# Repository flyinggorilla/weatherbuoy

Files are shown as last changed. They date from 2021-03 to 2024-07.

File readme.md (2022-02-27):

# Weather Buoy - ESP32 4G/LTE Solar
* On-water solar powered autonomous wind and weather station
* ESP32, SIM7600E, GILL MaxiMet GMX501

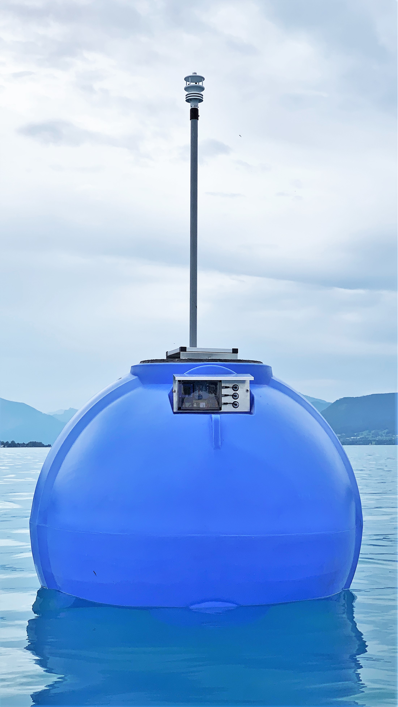
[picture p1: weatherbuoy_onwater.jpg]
weather buoy on water

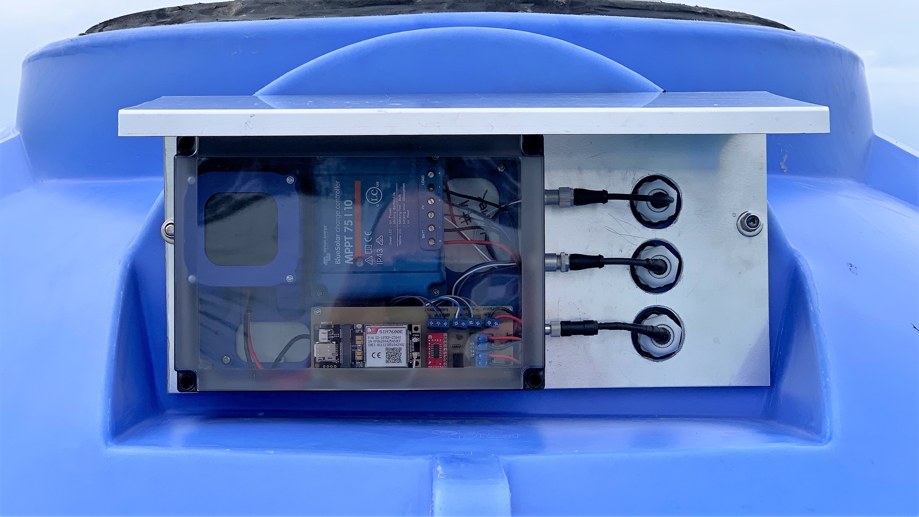
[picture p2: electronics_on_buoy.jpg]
electronics mounted on buoy with sun shield


<br>

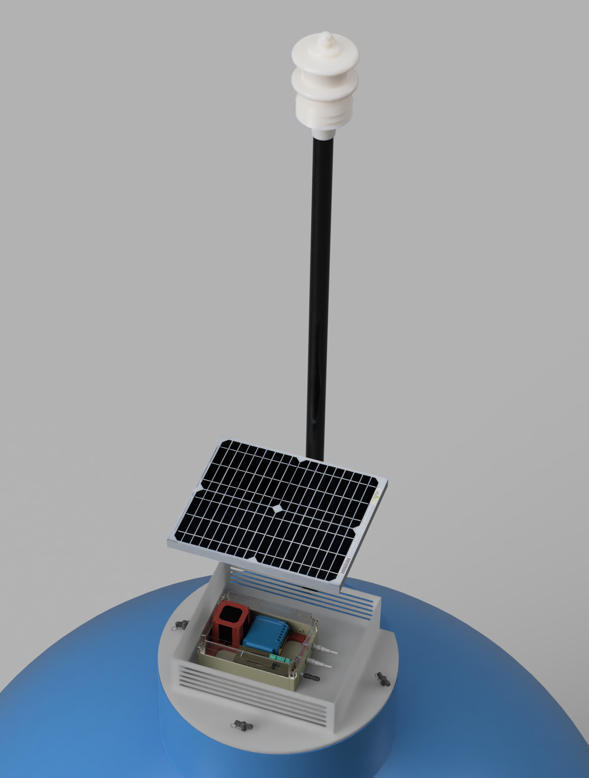
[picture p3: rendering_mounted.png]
rendering

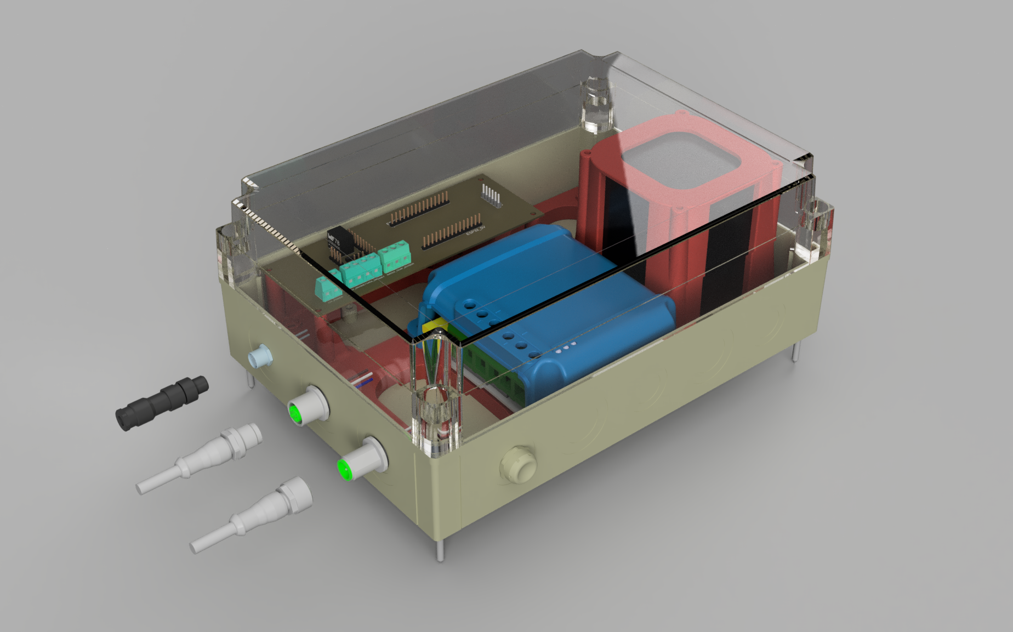
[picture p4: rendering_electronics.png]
rendering electronics

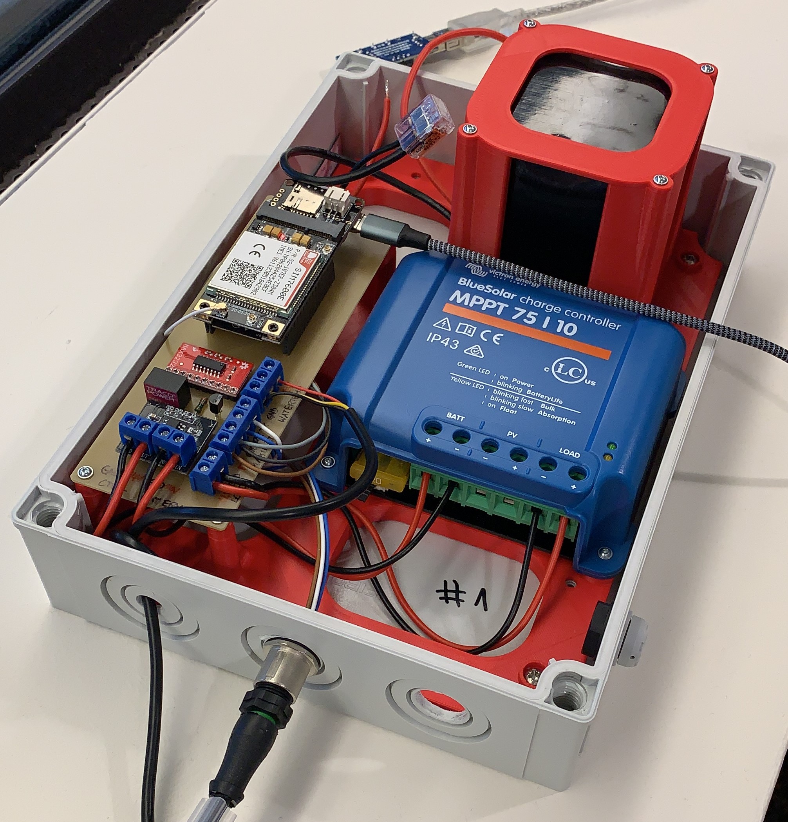
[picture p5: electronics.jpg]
electronics

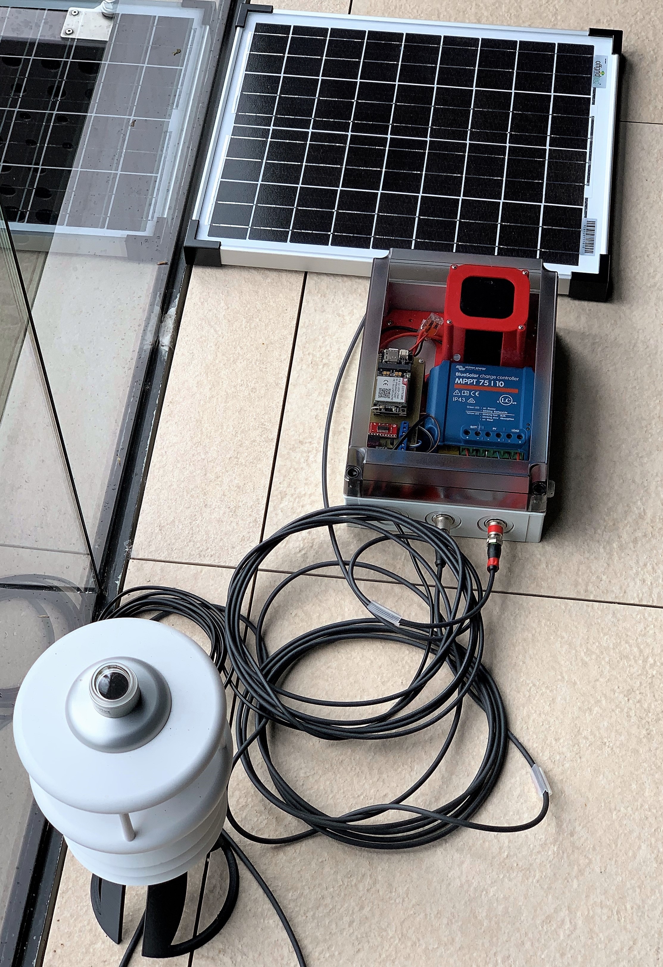
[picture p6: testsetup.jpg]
test setup
 

## Electronics part list

| Part | Description | Links | Cost (ex. delivery) |
|-|-|-|-|
| Waterproof housing | Fibox PCM200/100T, 255x180x100 Polycarbonat | [Fibox 6016927](https://www.fibox.de//catalog/64/product/183/6016927_GER1.html), [conrad](https://www.conrad.at/de/p/fibox-pcm-200-100-t-6016927-universal-gehaeuse-255-x-180-x-100-polycarbonat-lichtgrau-ral-7035-1-st-521203.html) | EUR 46 |
| Weather station | Gill MaxiMet: ultrasonic windspeed/direction, compass, solar radiation | [GILL MaxiMet GMX501](http://gillinstruments.com/data/datasheets/1957-009%20Maximet-gmx501%20Iss%207.pdf) Note: GMX200 costs half, just lacks solar| EUR 1500-3000 |
| Microcontroller |  Lilygo ESP32 | [LILYGO® TTGO T-PCIE ESP32-WROVER-B](http://www.lilygo.cn/prod_view.aspx?TypeId=50044&Id=1313&FId=t3:50044:3) | EUR 10 |
| 4G/LTE Modem  | SimCom 7600 | [PCIE-SIM7600E Module](http://www.lilygo.cn/prod_view.aspx?TypeId=50044&Id=1313&FId=t3:50044:3)  |  EUR 30 |
| Solar panel | 12V, 20W, monocrystalline, water proof IP65 | [Offgridtec](https://www.offgridtec.com/en/offgridtec-20w-mono-solarpanel-12v.html)| EUR 27 |
| Solar charging controller 12V | LiFePo4 capable, 5V power for microcontroller | [Victron Bluesolar, MPPT, 75/10](https://www.victronenergy.com/solar-charge-controllers/mppt7510) | EUR 80 |
| RS232 to TTL converter | MAX3232 to convert weatherstation's RS232 to 3.3V serial | [Sparkfun MAX3232 tranceiver breakout](https://www.sparkfun.com/products/11189) | EUR 5 |
| Voltage/Current sensor | MAX471 module, uses ESP32 ADC as there is no serial available to connect the ESP32 to the Victron Solar charger  | [MAX471 module with voltage divider](https://www.aliexpress.com/w/wholesale-max471-module.html), [MAX471 datasheet](https://www.maximintegrated.com/en/products/analog/amplifiers/MAX471.html) | ~EUR 2 |
| Water Temperature sensor | DS18B20 cable | [DS18B20 cable](https://www.az-delivery.de/en/products/2er-set-ds18b20-mit-3m-kabel?variant=19385240518752) | ~EUR 3 |
| On-Board Temperature sensor | DS18B20 TSO module | [DS18B20 TSO](https://www.az-delivery.de/en/products/5ersetds18b20?_pos=2&_sid=9a9ed3862&_ss=r) | ~EUR 1
| Battery | LiFePo4, 12V, 6Ah, 4S1P, including BMS | [Jubatec](https://www.jubatec.net/lifepo4-akku-12v-6ah-mit-bms-batterie-management-system_4652) | EUR 60 |
| 5V Power | convert ~14V Battery voltage to 5V for ESP32 |  [TracoPower TSR 1-2450 DC/DC-Wandler, 24V/DC 5V/DC 1A 6W](https://www.tracopower.com/int/model/tsr-1-2450) | EUR 6 |
| M12 male front-mount | Solar panel power, 4-pins, 2 pins combined to double current of 4A per pin | [7000-13501-9710050](https://shop.murrelektronik.de/en/Connection-Technology/Flange-Connectors/Signal/M12-male-receptacle-A-cod-front-mount-7000-13501-9710050.html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) | EUR 10 |
| M12 female with cable | Solar panel power, 4-pins, 2 pins combined to double current of 4A per pin, soldered to solar panel | [7000-12221-6340200](https://shop.murrelektronik.de/en/Connection-Technology/With-open-ended-wires/Signal/M12-female-0-with-cable-7000-12221-6340200.html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) | EUR 10 |
| M8 male connector | soldered to Water temperature sensor cable | [7000-08401-0000000](https://shop.murrelektronik.de/en/Connection-Technology/Field-wireable/Signal/M8-MALE-0-FIELD-WIREABLE-SOLDER-PINS-7000-08401-0000000.html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) | EUR 11 |
| M8 female front-mount 3-pin | Water temperature sensor | [7000-08571-9700050](https://shop.murrelektronik.de/en/Connection-Technology/Flange-Connectors/Signal/M8-FEMALE-FLANGE-PLUG-A-CODED-FRONT-MOUNT-7000-08571-9700050.html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) | EUR 9 |
| M12 female front-mount 5-pin | RS232 data and 5V power connection to Maximet weatherstation | [7000-13561-9720100](https://shop.murrelektronik.de/en/Connection-Technology/Flange-Connectors/Signal/M12-female-receptacle-A-cod-front-mount-7000-13561-9720100.html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)| EUR 12 |
| M12 male connector cable 5-pin | RS232 data and 5V power connection to Maximet weatherstation with Maximet specific IP67 soldered Connector | [7000-12041-6250300](https://shop.murrelektronik.de/en/Connection-Technology/With-open-ended-wires/Signal/M12-male-0-with-cable-7000-12041-6250300.html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) | EUR 11 |
| Pressure compensation unit | Wiska EVPS - Pressure compensation unit, VentPLUG, plastic, metric | [WISKA EVPS 40 10106593](https://www.wiska.com/de/143/pde/10102369/evps-12.html) | EUR 4 |

## wiring
[wiring diagrams](wiring/readme.md)

## CAD: 3D-print & PCB

files are in the folder [/cad](cad)

[System: Fusion 360 live model](https://a360.co/3yyAmHY)
[PCB: Fusion 360 live model](https://a360.co/3zrHFRN)

how to order a PCB:
* choose a PCB manufacturer. recommendation: https://www.eurocircuits.com/ 
* upload __weatherbuoy pcb.brd__ to e.g. eurocircuits to order your PCB

## firmware
* built with ESP-IDF Version 4.3 or later
* adds software components for
  * Cellular handling for SimCom 7600E Modem
  * Max417 current/voltage measurement
  * Comfortable/safer Strings
  * reading/parsing Gill Maximet data from serial interface
* new as of February 2022:
  * remotely configuring Gill Maximet wind/weather stations
  * NMEA2000 data output for a real-time Display e.g. Garmin GNX130
  * SMS and Buzzer alerting based on GPS geofence, tilt sensor, and Maximet unplugging
  * Use exactly same electronics also to simulate a maximet station for testing purposes
  * upgraded to ESP-IDF 4.4
  * improved serial/UART handling to maximet and modem for performance and robustness

## Lilygo TTGP T-PCIE SIM7600E PIN usage
* UART0: RX: GPIO3, TX: GPIO1 (USB, logging, debugging)
* UART1: RX: GPI13, TX: GPIO14 (Maximet RS232)
* UART2: RX: GPIO16, TX: GPIO17 (SimCom Modem)
* ADC: GPIO39 (Max471, Voltage)
* ADC: GPIO34 (Max471, Current)
* TWAI: RX: GPIO22, TX: GPIO21 (I2C ports for driving NMEA2000 display)
* OUT: GPIO19 (Buzzer, up to max 70mA)

## SIM7600E modem firmware
* LE11B03SIM7600M21-A v1.12 B03 cannot be switched to LTE (works only as GSM modem) 
* LE11B04SIM7600M21-A v1.12 B04 works fine also in LTE mode
* LE20B04SIM7600M21-A v2.0  B04 works find also in LTE mode

  Lilygo Firmware upgrade instructions https://github.com/Xinyuan-LilyGO/LilyGo-T-PCIE/blob/master/doc/sim7600SA_update_firmware.md

## troubleshooting

### cannot flash via serial/USB anymore
* remove serial connection to Maximet (or turn off/reset Maximet/Simulator device)
  https://esp32.com/viewtopic.php?t=1205

### observing weird crashes, especially after changing git branches
* completely delete the build folder and perform a 100% clean build
 https://esp32.com/viewtopic.php?t=1205

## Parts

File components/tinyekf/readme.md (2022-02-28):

# THIS MODULE IS WORK IN PROGRESS

# TinyEKF: Extended Kalman Filter 
* based on Simon D. Levy TinyEKF https://github.com/simondlevy/TinyEKF
* modified for GPS data and ESP32
* tutorial on kalman filters: https://simondlevy.academic.wlu.edu/kalman-tutorial/

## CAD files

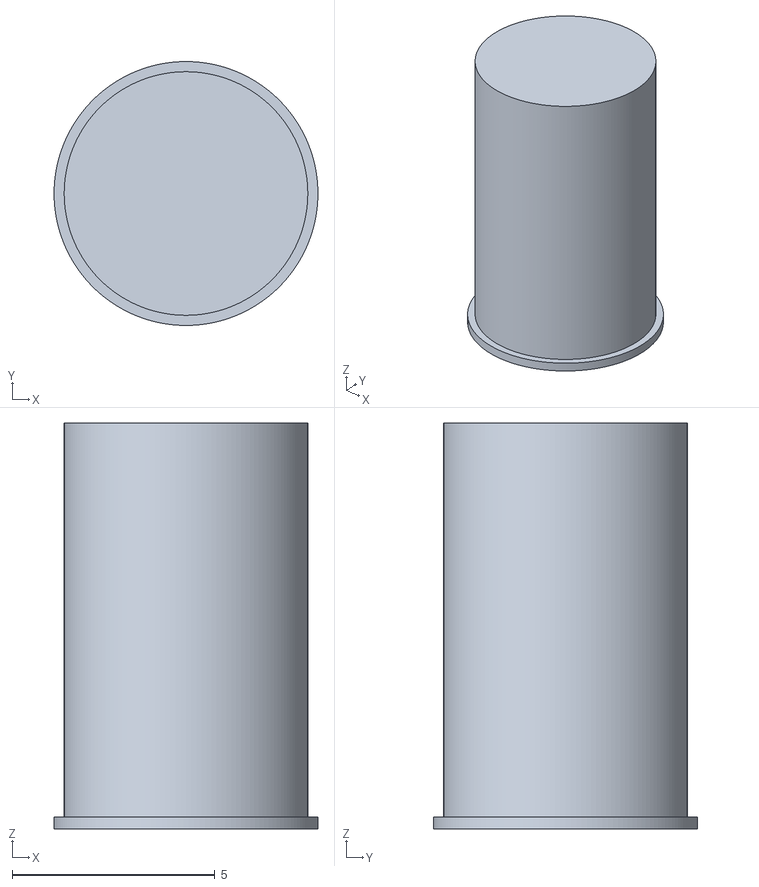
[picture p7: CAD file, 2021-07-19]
cad/solarpanel blind cable plug 6mm.stl
6.50 x 6.50 x 10.0

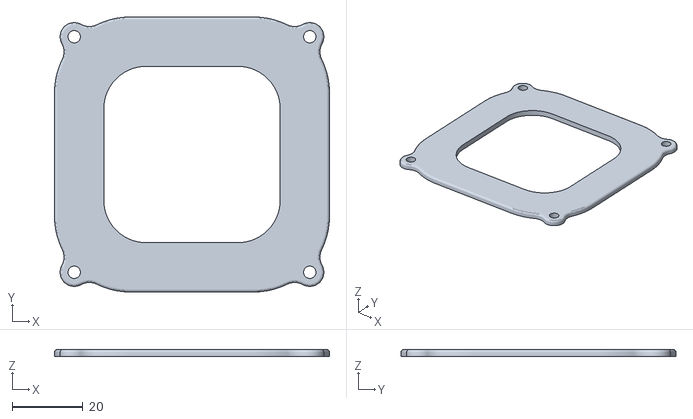
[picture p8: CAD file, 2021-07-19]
cad/weatherbuoy battery lid.stl
78.0 x 78.0 x 2.00

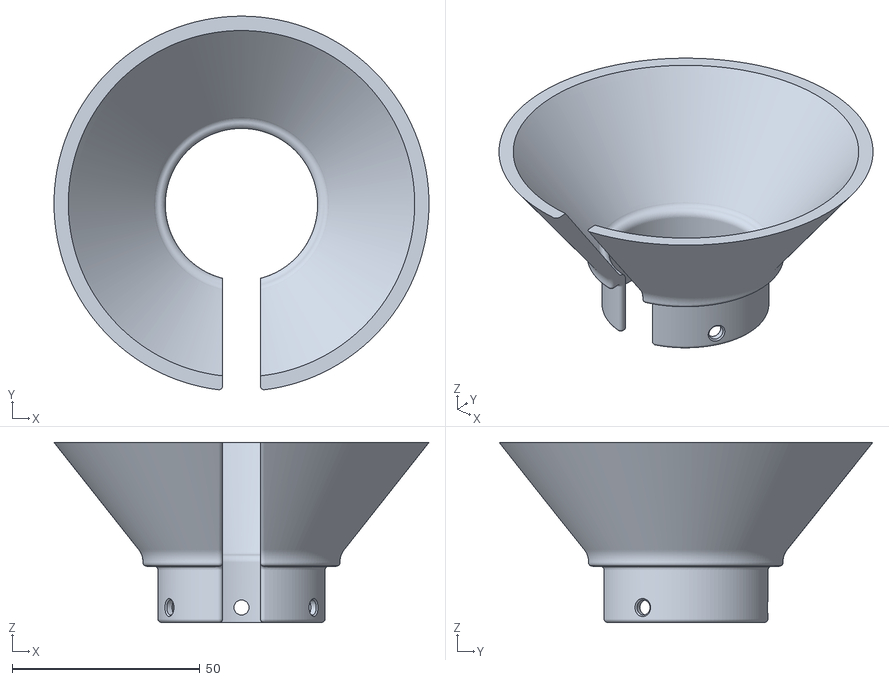
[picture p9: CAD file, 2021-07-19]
cad/maximet stand.stl
100.0 x 99.6 x 48.0

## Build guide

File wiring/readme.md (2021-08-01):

#wiring
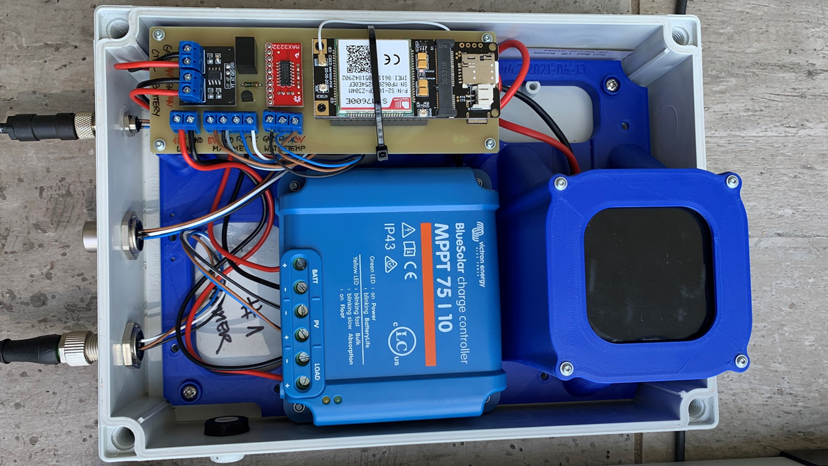
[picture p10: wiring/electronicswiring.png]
wiring

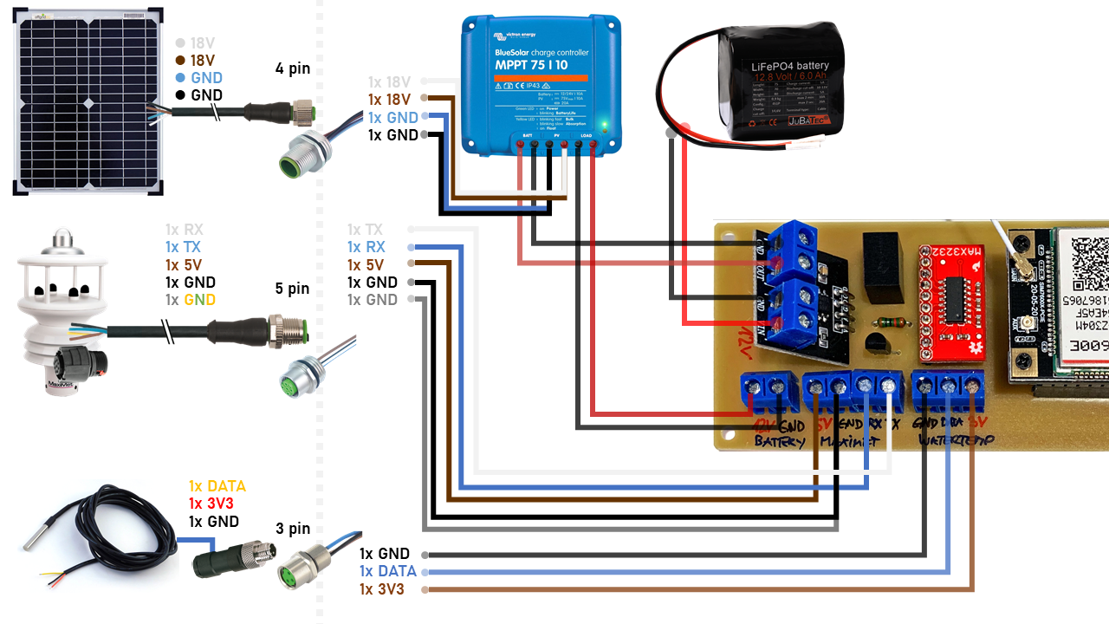
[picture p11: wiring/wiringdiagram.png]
wiring

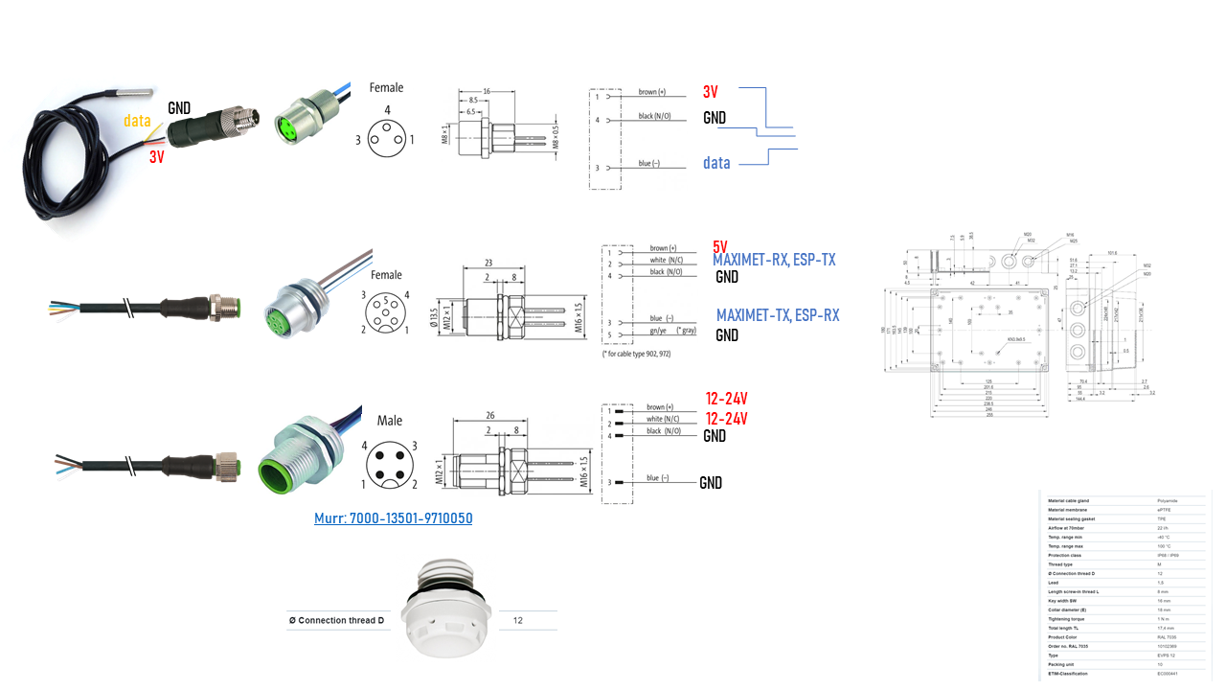
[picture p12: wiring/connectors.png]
connectors

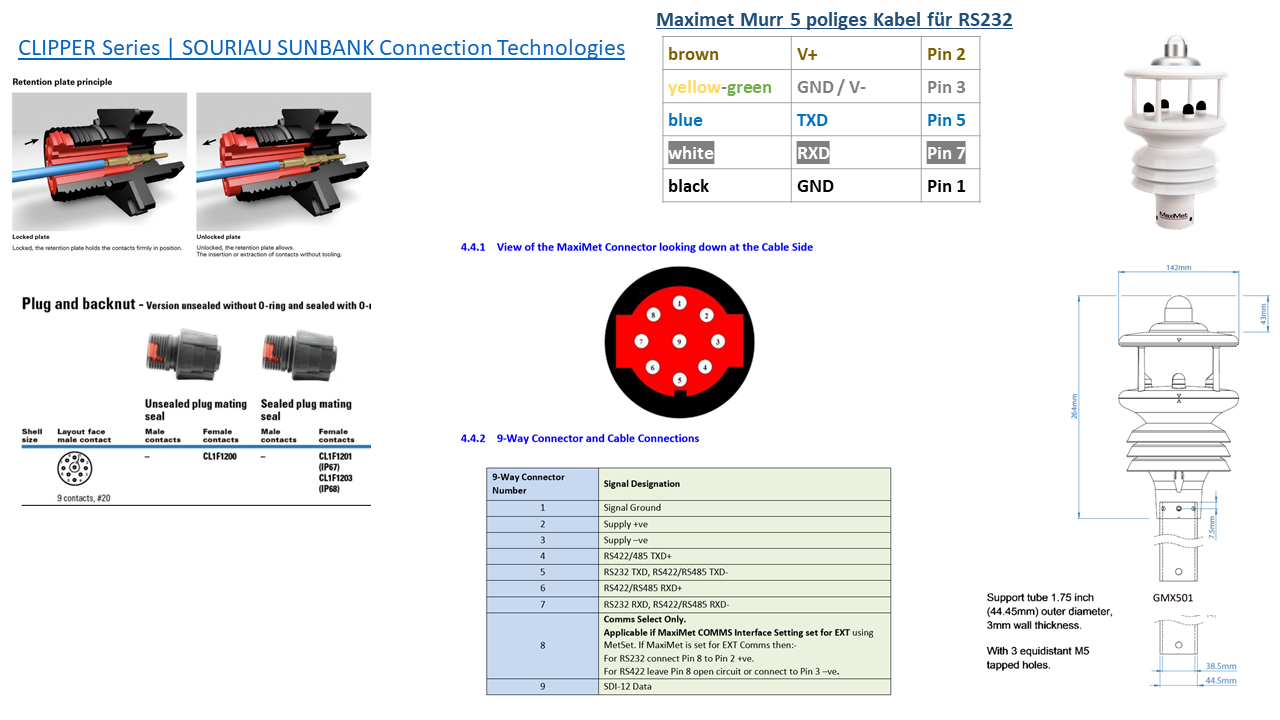
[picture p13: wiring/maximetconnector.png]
maximetconnector

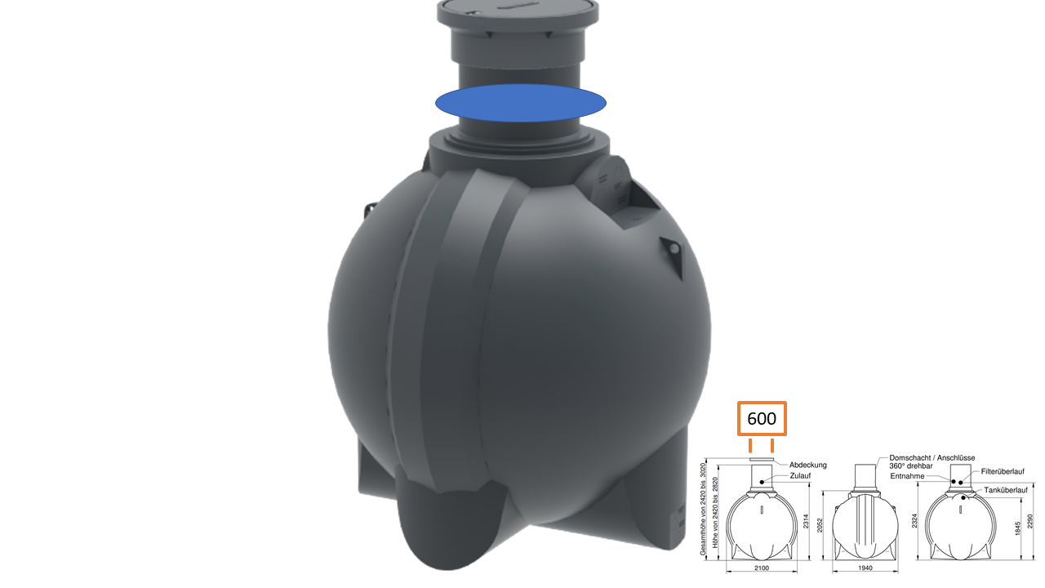
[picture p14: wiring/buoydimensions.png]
buoy

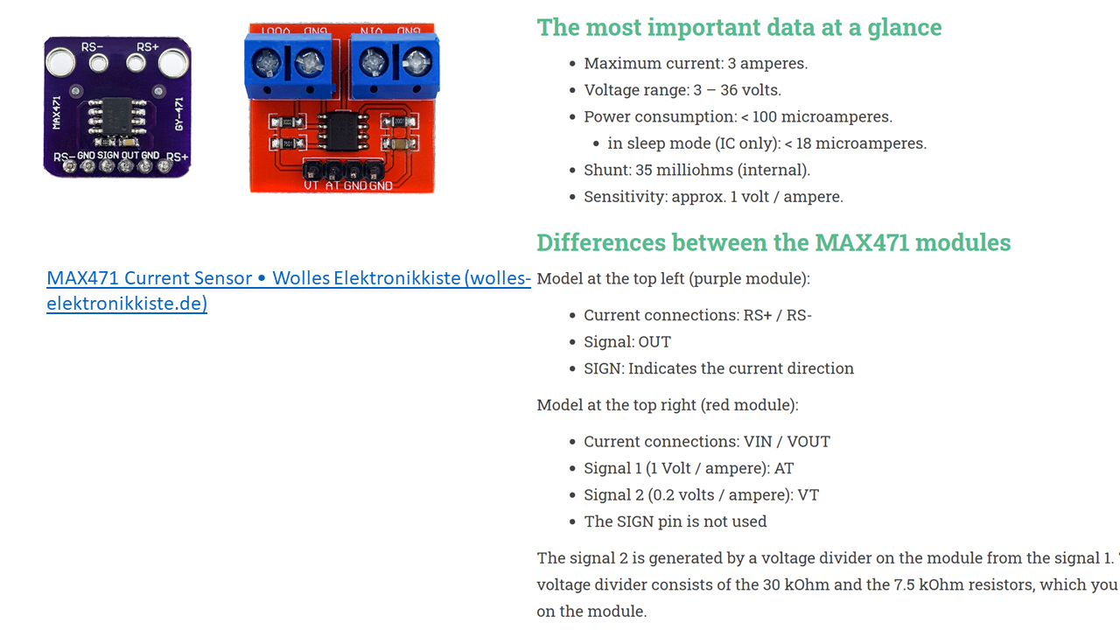
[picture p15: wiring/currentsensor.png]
current sensor

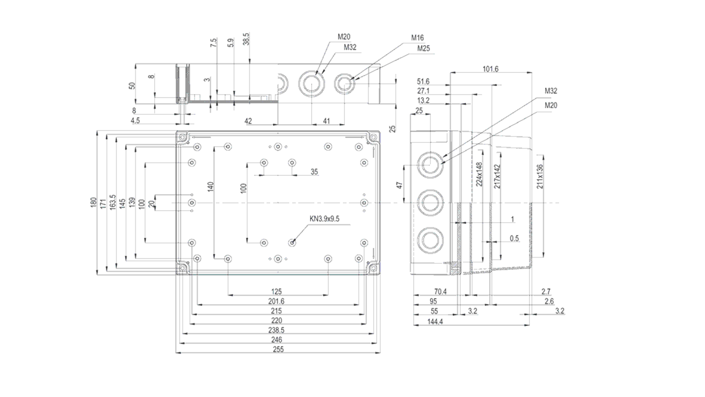
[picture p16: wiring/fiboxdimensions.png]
fibox

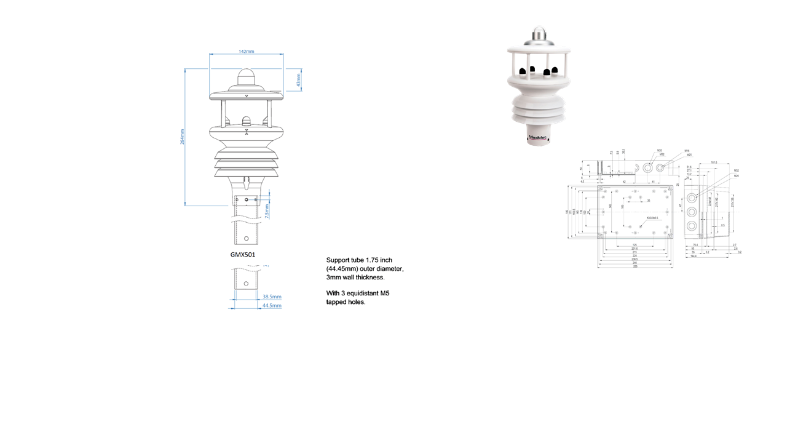
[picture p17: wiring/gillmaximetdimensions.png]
maximet

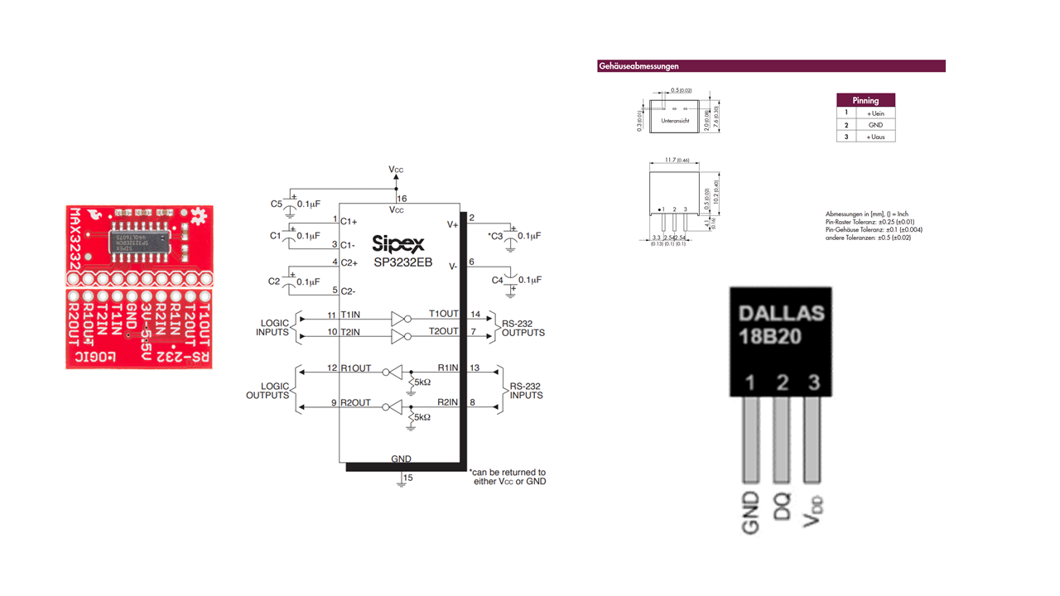
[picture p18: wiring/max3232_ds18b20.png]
max3232

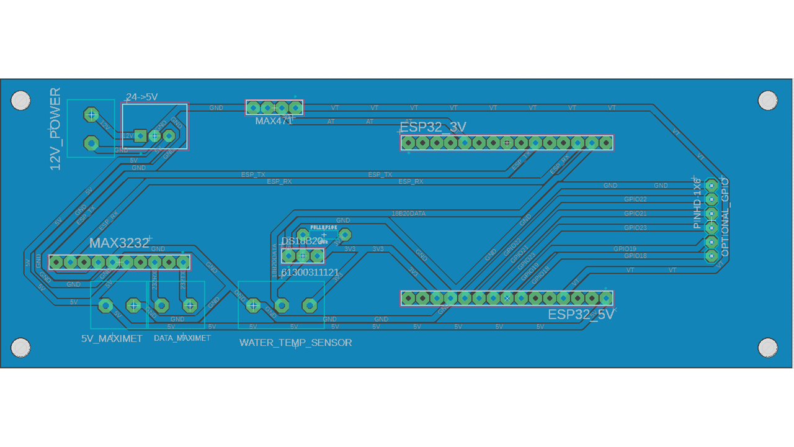
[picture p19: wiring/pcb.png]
pcb

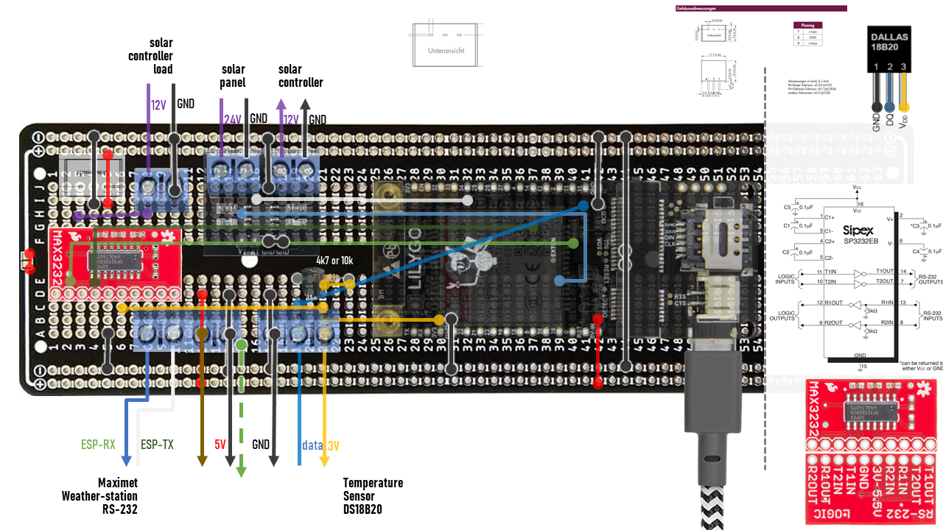
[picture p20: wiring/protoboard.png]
protoboard


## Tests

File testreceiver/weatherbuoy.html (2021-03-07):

refresh

# Weatherbuoy Management Console

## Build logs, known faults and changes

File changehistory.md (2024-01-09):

# History

## 2022-12-19

* Enabled IPv4 & IPv6 fragmented IP reassembly (finally eliminated http/lwip client sock=54 errors)
* disable: DHCP: Perform ARP check on any offered address

## 2023-01-02

* disabled gratituous ARP sending on LWIP
* no longer smooth time upates, as that caused problems after restart
* reset UART receive buffer after netif action stops, and wait for TX fifo clearance
* updated to ESP-IDF v4.4.3

## 20230104.1923

* set UART send buffer to 0 for blocking send calls. to ensure this isnt causing TCP/IP connect issues. at least it frees memory

## 20230105.1306

* added quick HTTP client connect failure retry without restarting Modem

## 20230325.1259

* added Maximet %% command and print to log for exact model number
* updated to ESP-IDF v4.4.4

## 20230404.0823

* added Modem power cycling after too many HTTP connectivity issues
* added extended Software restart reason, for diagnostics

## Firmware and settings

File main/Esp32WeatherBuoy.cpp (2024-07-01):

// #define LOG_LOCAL_LEVEL ESP_LOG_DEBUG
#include "sdkconfig.h"
#include "esp_system.h"
#include "esp_log.h"
#include "esp_event.h"
#include "Esp32WeatherBuoy.h"
#include "Config.h"
#include "SendData.h"
#include "Maximet.h"
#include "MaximetSimulator.h"
#include "Watchdog.h"
#include "Wifi.h"
#include "Cellular.h"
#include "Max471Meter.h"
#include "TemperatureSensors.h"
#include "nvs_flash.h"
#include "esp_ota_ops.h"
#include "NmeaDisplay.h"
#include "Alarm.h"
#include "RtcVariables.h"

static const char tag[] = "WeatherBuoy";

// ------------------------------------------
// change device in Menuconfig->Cellular
// ------------------------------------------
#ifdef CONFIG_LILYGO_TTGO_TCALL14_SIM800
// LILYGO TTGO T-Call V1.4 SIM800
// ADC ----------------------------
// Using ADC1 with possible GPIO: 32, 34, 35, 36, 39
#define CONFIG_MAX471METER_GPIO_VOLTAGE 35
#define CONFIG_MAX471METER_GPIO_CURRENT 34

// MAXIMET Serial
// dont use default RX/TX GPIO as it is needed for console output.
// dont use conflicting internal flash and boot-blocking GPIO 0, 1, 2, 3, 4, 5, 6, 7, 8, 9, 10, 12
#define CONFIG_WEATHERBUOY_READMAXIMET_RX_PIN 13
#define CONFIG_WEATHERBUOY_READMAXIMET_TX_PIN 14
#elif CONFIG_LILYGO_TTGO_TPCIE_SIM7600
// LILYGO® TTGO T-PCIE SIM7600
// ADC ----------------------------
// Using ADC1 with possible GPIO: 32, 34, 35, 39 (note GPIO 33 did not work)
#define CONFIG_MAX471METER_GPIO_VOLTAGE 39
#define CONFIG_MAX471METER_GPIO_CURRENT 34

// MAXIMET Serial
// dont use default RX/TX GPIO as it is needed for console output.
// dont use conflicting internal flash and boot-blocking GPIO 0, 1, 2, 3, 4, 5, 6, 7, 8, 9, 10, 12
#define CONFIG_WEATHERBUOY_READMAXIMET_RX_PIN 13
#define CONFIG_WEATHERBUOY_READMAXIMET_TX_PIN 14

// OneWire protocol for temperature sensors DS18B20
#define CONFIG_TEMPERATURESENSOR_GPIO_ONEWIRE 15
// Test setup DS18B20:
// Breadboard TOS ROM code: "303c01e076e5f528"
// Waterproof sensor ROM code: "220120639e26f028"
#endif

#define NMEA
#ifdef NMEA
// I2C Pins
#define CONFIG_I2C_SCL_PIN 22
#define CONFIG_I2C_SDA_PIN 21
// I2C Pins used for TWAI (NMEA over CAN bus)
#define CONFIG_NMEA_TWAI_RX_PIN GPIO_NUM_22
#define CONFIG_NMEA_TWAI_TX_PIN GPIO_NUM_21
#define CONFIG_NMEA_TWAI_POWER_PIN GPIO_NUM_23 // power the chip through GPIO, so CAN BUS chip stays powered down during boot
#endif

// Optionally drive an Alarm Buzzer at following GPIO (max 30mA for standard GPIO, but this one can with proper config drive up to 70mA)
#define CONFIG_ALARM_BUZZER_PIN GPIO_NUM_19

// Restart ESP32 if there is not data being successfully sent within this period.
#define CONFIG_WATCHDOG_SECONDS 60 * 65   // 65min - if hourly send including retries fail,then lets restart
#define CONFIG_SOLARRADIATIONMIN_DAYTIME 2 // >2W/m2 solar radiation to declare DAYTIME



Esp32WeatherBuoy::Esp32WeatherBuoy()
{
}
Esp32WeatherBuoy::~Esp32WeatherBuoy()
{
}



extern "C"
{
    void app_main();
}

void app_main()
{
    ESP_ERROR_CHECK(esp_netif_init());
    Esp32WeatherBuoy esp32WeatherBuoy;
    esp32WeatherBuoy.Start();
    esp_restart();
}

void TestHttp();
void TestATCommands(Cellular &cellular);

#include "VelocityVector.h"
void TestVelocityVector();



void Esp32WeatherBuoy::Start()
{
    RtcVariables::Init();

#if LOG_LOCAL_LEVEL >= LOG_DEFAULT_LEVEL_DEBUG || CONFIG_LOG_DEFAULT_LEVEL >= LOG_DEFAULT_LEVEL_DEBUG
    esp_log_level_set("Cellular", ESP_LOG_DEBUG);
    esp_log_level_set("Wifi", ESP_LOG_DEBUG);
    esp_log_level_set("Alarm", ESP_LOG_DEBUG);
    esp_log_level_set("Maximet", ESP_LOG_INFO);
    esp_log_level_set("MaximetSimulator", ESP_LOG_DEBUG);
    esp_log_level_set("Serial", ESP_LOG_DEBUG);
    esp_log_level_set("HTTP_CLIENT", ESP_LOG_VERBOSE);
    esp_log_level_set("esp-netif_lwip-ppp", ESP_LOG_WARN);
#endif

    ESP_LOGI(tag, "Atterwind WeatherBuoy starting!");
    if (!mConfig.Load())
    {
        ESP_LOGE(tag, "Error, could not load configuration.");
    }

    if (!mConfig.msCellularApn.length() && strlen(CONFIG_WEATHERBUOY_CELLULAR_APN))
    {
        mConfig.msCellularApn = CONFIG_WEATHERBUOY_CELLULAR_APN;
        mConfig.Save();
        ESP_LOGW(tag, "Saved firmware default APN configuration! %s", mConfig.msCellularApn.c_str());
    }

    if (mConfig.miSimulator)
    {
        ESP_LOGI(tag, "Maximet Simulation: GMX%d%s", mConfig.miSimulator / 10, mConfig.miSimulator % 10 ? "GPS" : "");
    }

    if (mConfig.mbNmeaDisplay)
    {
        ESP_LOGI(tag, "NMEA2000 Display output activated (i.e. Garmin GNX130).");
    }

#ifdef TESTVELOCITYVECTOR
    TestVelocityVector();
#endif

    int watchdogSeconds = CONFIG_WATCHDOG_SECONDS;
    Watchdog watchdog(watchdogSeconds);
    ESP_LOGI(tag, "Watchdog started and adjusted to %d seconds.", watchdogSeconds);

    TemperatureSensors tempSensors(mConfig);
    tempSensors.Init(CONFIG_TEMPERATURESENSOR_GPIO_ONEWIRE);

    ESP_LOGI(tag, "Hostname: %s", mConfig.msHostname.c_str());
    // ESP_LOGI(tag, "Target URL: %s", mConfig.msTargetUrl.c_str());
    ESP_LOGI(tag, "Target URL: %s", CONFIG_WEATHERBUOY_TARGET_URL);
    ESP_LOGI(tag, "App Version: %s", esp_ota_get_app_description()->version);

    Max471Meter max471Meter(CONFIG_MAX471METER_GPIO_VOLTAGE, CONFIG_MAX471METER_GPIO_CURRENT);
    ESP_LOGI(tag, "Max471Meter: voltage %d mV, current %d mA", max471Meter.Voltage(), max471Meter.Current());

    DataQueue dataQueue;

    // allocate NMEA2000 display output on heap as moving averages require some memory
    if (mConfig.mbNmeaDisplay)
    {
        mpDisplay = new NmeaDisplay(CONFIG_NMEA_TWAI_TX_PIN, CONFIG_NMEA_TWAI_RX_PIN, CONFIG_NMEA_TWAI_POWER_PIN ,dataQueue);
        mpDisplay->Start();

        tempSensors.Read();  // note, this causes approx 700ms delay
        unsigned int voltage = max471Meter.Voltage();
        unsigned int current = max471Meter.Current();
        float boardtemp = tempSensors.GetBoardTemp();
        mpDisplay->SetSystemInfo(voltage, current, boardtemp);
    }

    // start Maximet wind/weather data reading
    int maximetRxPin = CONFIG_WEATHERBUOY_READMAXIMET_RX_PIN;
    int maximetTxPin = CONFIG_WEATHERBUOY_READMAXIMET_TX_PIN;
    Maximet maximet(dataQueue);
    if (!mConfig.miSimulator)
    {
        maximet.Start(maximetRxPin, maximetTxPin);
    }

    
    //ESP_LOGE(tag, "remove http client logging!");

    //ESP_LOGE(tag, "remove simulator check!");
    //if (!mConfig.miSimulator && mCellular.Init())

    // detect available Simcom 7600E Modem, such as on Lillygo PCI board
    if (mCellular.Init(mConfig.msCellularApn, mConfig.msCellularUser, mConfig.msCellularPass, mConfig.msCellularOperator, mConfig.miCellularNetwork) && mCellular.PowerUp())
    {
        mOnlineMode = MODE_CELLULAR;

        // mCellular.ReadSMS(); // use only during firmware setup to receive a SIM based code
        // AT+CMGD Delete Message (with option 4 to delete all)
    }
    else // try wifi if configured
    {
         if (mConfig.msSTASsid.length())
        {
            // config.msSTASsid = "";
            // config.msSTAPass = "";
            // config.msTargetUrl = "http://10.10.14.195:3000/weatherbuoy";
            // config.Save();
            ESP_LOGI(tag, "sssi %s, pass %d characters, host %s", mConfig.msSTASsid.c_str(), mConfig.msSTAPass.length(), mConfig.msHostname.c_str());
            mWifi.StartSTAMode(mConfig.msSTASsid, mConfig.msSTAPass, mConfig.msHostname);
            mWifi.StartTimeSync(mConfig.msNtpServer);
            ESP_LOGI(tag, "NTP Time Syncronization enabled: %s", mConfig.msNtpServer.c_str());

            mOnlineMode = MODE_WIFISTA;
        }
        else if (mConfig.msAPSsid.length())
        {
            ESP_LOGI(tag, "sssi %s pass %s host %s", mConfig.msAPSsid.c_str(), mConfig.msAPPass.c_str(), mConfig.msHostname.c_str());
            mWifi.StartAPMode(mConfig.msAPSsid, mConfig.msAPPass, mConfig.msHostname);
            mOnlineMode = MODE_WIFIAP;
        }
        else
        {
            ESP_LOGW(tag, "Staying offline.");
            mOnlineMode = MODE_OFFLINE;
        }
    }

    SendData sendData(mConfig, dataQueue, mCellular, watchdog, maximet);

    if (mConfig.miSimulator)
    {
        // run Simulator
        ESP_LOGI(tag, "Starting: Gill Maximet Wind Sensor Simulator GMX%d%s", mConfig.miSimulator / 10, mConfig.miSimulator % 10 ? "GPS" : "");
        RunSimulator(tempSensors, dataQueue, max471Meter, sendData, maximet, static_cast<Maximet::Model>(mConfig.miSimulator));
    }
    else
    {
        // run Weatherbuoy and Startboat
        Alarm *pAlarm = nullptr;
        if (mConfig.mbAlarmSound || mConfig.msAlarmSms.length())
        {
            ESP_LOGI(tag, "Starting: Alarm system");
            pAlarm = new Alarm(dataQueue, mConfig, CONFIG_ALARM_BUZZER_PIN);
            pAlarm->Start();
        }

        Run(tempSensors, dataQueue, max471Meter, sendData, maximet, pAlarm);
    }
}

void Esp32WeatherBuoy::HandleAlarm(Alarm *pAlarm)
{
    if (mOnlineMode != MODE_CELLULAR || !pAlarm || !pAlarm->IsAlarm())
        return;

    ESP_LOGI(tag, "switching to full power mode next...");
    if (!mCellular.SwitchToFullPowerMode())
    {
        ESP_LOGE(tag, "SEVERE, Switching to full power mode failed. Restarting.");
        RtcVariables::SetExtendedResetReason(RtcVariables::EXTENDED_RESETREASON_MODEMFULLPOWERFAILED);
        esp_restart();
        return;
    }

    //vTaskDelay(100 / portTICK_PERIOD_MS);

    ESP_LOGI(tag, "SMS Numbers: %s", mConfig.msAlarmSms.c_str());
    String msg;
    //String numbers(mConfig.msAlarmSms); // copy phone numbers, so to split later
    msg = "ALARM ";
    msg += mConfig.msHostname;
    msg += "!\r\n";
    msg += pAlarm->GetAlarmInfo();
    msg += "\r\n";

    int startPos = 0; // start of phone number
    int endPos = 0; // end of phone number, before position of delimiter or end of string
    const int length = mConfig.msAlarmSms.length();
    int sent = 0;
    while (startPos < length)
    {
        endPos = mConfig.msAlarmSms.indexOf(',', startPos);
        if (endPos < 0)
        {
            endPos = length;
        } 
        String to = mConfig.msAlarmSms.substring(startPos, endPos);
        to.trim();

        if (to.length())
        {
            //ESP_LOGI(tag, "Sending SMS: to: %s msg: %s", to.c_str(), msg.c_str());
            if (mCellular.SendSMS(to, msg))
            {
                sent++;
            }
        } else  {
            break;
        }
        startPos = endPos + 1;
    }

    pAlarm->ConfirmAlarm();
};

void Esp32WeatherBuoy::Run(TemperatureSensors &tempSensors, DataQueue &dataQueue, Max471Meter &max471Meter, SendData &sendData, Maximet &maximet, Alarm *pAlarm)
{
    ESP_LOGI(tag, "Running: %s, Maximet: %s", 
            mpDisplay ? "Racing Committee Boat with Garmin GNX130 NMEA200 Display" : "Weatherbuoy", 
            maximet.GetConfig().sUserinfo.c_str());

    String tempSensorRomCodes = tempSensors.GetRomCodes();

    bool bDiagnostics;
    bool bDiagnosticsAtStartup = true;
    unsigned int lastSendTimestamp = 0;
    unsigned int lastDiagnosticsTimestamp = 0;

    int secondsToSleep = 0;

    int logInfoSeconds = 0;

    while (true)
    {
        HandleAlarm(pAlarm); // check for alarm before and after waiting for the queue to minimize latency
        vTaskDelay(1 * 1000 / portTICK_PERIOD_MS);
        bool isMaximetData = dataQueue.WaitForData(60);
        HandleAlarm(pAlarm); // check for alarm
        unsigned int secondsSinceLastSend;
        unsigned int secondsSinceLastDiagnostics;

        // keep modem sleeping unless time to last send elapsed
        unsigned int uptimeSeconds = (unsigned int)(esp_timer_get_time() / 1000000); // seconds since start
        secondsSinceLastSend = uptimeSeconds - lastSendTimestamp;
        if (secondsToSleep > secondsSinceLastSend)
        {
            if (logInfoSeconds == 0)
            {
                ESP_LOGI(tag, "Power management sleep: %d, Measurements in queue: %d", secondsToSleep - secondsSinceLastSend, dataQueue.GetQueueLength());
                logInfoSeconds = 60;
            }
            logInfoSeconds--;
            continue;
        }
        lastSendTimestamp = uptimeSeconds;

        // when sending, add diagnostics information after 300 seconds
        secondsSinceLastDiagnostics = uptimeSeconds - lastDiagnosticsTimestamp;
        if (secondsSinceLastDiagnostics > mConfig.miIntervalDiagnostics || bDiagnosticsAtStartup)
        {
            bDiagnostics = true;
            bDiagnosticsAtStartup = false;
            lastDiagnosticsTimestamp = uptimeSeconds;
        }
        else
        {
            bDiagnostics = false;
        }

        // check if maximeta or info data should be sent at all
        if (!isMaximetData && !bDiagnostics)
        {
            continue;
        }

        tempSensors.Read();  // note, this causes approx 700ms delay
        unsigned int voltage = max471Meter.Voltage();
        unsigned int current = max471Meter.Current();
        float boardtemp = tempSensors.GetBoardTemp();
        float watertemp = tempSensors.GetWaterTemp();

        if (mpDisplay) {
            mpDisplay->SetSystemInfo(voltage, current, boardtemp);
        }

        if (mOnlineMode == MODE_CELLULAR)
        {
            const int MAX_ATTEMPTS = 5;
            int attempts = MAX_ATTEMPTS;
            bool prepared = false;
            do
            {
                ESP_LOGI(tag, "Switching to full power mode next...");
                if (!mCellular.SwitchToFullPowerMode())
                {
                    ESP_LOGE(tag, "SEVERE, Switching to full power mode failed. Remaining attempts: %i", attempts);
                    if (attempts < MAX_ATTEMPTS) {
                        RtcVariables::IncModemRestarts();
                        mCellular.PowerDown();
                    }
                    continue;
                }

                ESP_LOGI(tag, "Switching to PPP mode next...");
                if (!mCellular.SwitchToPppMode())
                {
                    ESP_LOGE(tag, "SEVERE, Failed to switch to PPP mode. Remaining attempts: %i", attempts);
                    if (attempts < MAX_ATTEMPTS) {
                        RtcVariables::IncModemRestarts();
                        mCellular.PowerDown();
                    }
                    continue;
                };

                if (!prepared)
                {
                    // read maximet data queue and create a HTTP POST message
                    sendData.PrepareHttpPost(voltage, current, boardtemp, watertemp, bDiagnostics, mOnlineMode, tempSensorRomCodes);
                    prepared = true;
                }

                bool httpPostSucceeded = false;
                int httpAttempts = 3;
                do {
                    if(sendData.PerformHttpPost()) {
                        httpPostSucceeded = true;
                        break;
                    } else {
                        ESP_LOGE(tag, "HTTP Post request failed. Retrying HTTP request. Remaining attempts: %i", httpAttempts);
                        vTaskDelay(1000/portTICK_PERIOD_MS); // wait one second
                    }
                } while (--httpAttempts);

                if (httpPostSucceeded)
                {
                    ESP_LOGI(tag, "Posting data succeeded. Switching to low power mode...");
                    mCellular.SwitchToSleepMode();

                    int duration = (unsigned int)(esp_timer_get_time() / 1000000) - uptimeSeconds;
                    ESP_LOGI(tag, "Total data send duration %is.", duration);
                    break;
                }
                else
                {
                    ESP_LOGE(tag, "Failed to perform HTTP Post. Power cycling modem. Remaining attempts: %i", attempts);
                    RtcVariables::IncModemRestarts();
                    mCellular.PowerDown();
                }

            } while (--attempts);

            if (attempts == 0) {
                RtcVariables::SetExtendedResetReason(RtcVariables::EXTENDED_RESETREASON_CONNECTIONRETRIES);
                ESP_LOGE(tag, "SEVERE, Too many attempts to connect to server failed. Restarting.");
                esp_restart();
            }
        }

        // display runs on power, so no worries about power management
        if (mpDisplay) 
        {
            secondsToSleep = mConfig.miIntervalDay;
            continue;
        }

        // Power Managment
        // -----------------------------------------------------------
        // determine nighttime by low solar radiation
        ESP_LOGI(tag, "Solarradiation: %d W/m2  Voltage: %.02fV", maximet.SolarRadiation(), voltage / 1000.0);
        if (maximet.SolarRadiation() > CONFIG_SOLARRADIATIONMIN_DAYTIME && voltage > 13100)
        {
            secondsToSleep = mConfig.miIntervalDay; // s;
            ESP_LOGI(tag, "Sending data at daytime interval every %d seconds", secondsToSleep);
        }
        else if (voltage > 12750)
        {
            secondsToSleep = mConfig.miIntervalNight; // s;
            ESP_LOGI(tag, "Sending data at nighttime interval every %d minutes", secondsToSleep / 60);
        }
        else
        { // got into low battery mode if voltage is below 12.75V
            secondsToSleep = mConfig.miIntervalLowbattery;
            ESP_LOGI(tag, "Sending data in low-battery mode every %d minutes", secondsToSleep / 60);
        }
    }
}

void Esp32WeatherBuoy::RunSimulator(TemperatureSensors &tempSensors, DataQueue &dataQueue, Max471Meter &max471Meter, SendData &sendData, Maximet &maximet, Maximet::Model model)
{
    MaximetSimulator simulator;
    int maximetRxPin = CONFIG_WEATHERBUOY_READMAXIMET_RX_PIN;
    int maximetTxPin = CONFIG_WEATHERBUOY_READMAXIMET_TX_PIN;
    // since no MODEM was found, we assume this is an Adafruit ESP32 Feather board, with different serial pins
    // comment those two lines if you use a Lillygo PCIE board without Modem
    maximetRxPin = 16;
    maximetTxPin = 17;

    simulator.Start(model, maximetRxPin, maximetTxPin);

    Data data;
    String tempSensorRomCodes = tempSensors.GetRomCodes();

    unsigned int maximetDataIntervalSeconds = 60;
    unsigned int httpPostDataIntervalSeconds = 30;
    unsigned int lastSendTimestamp = 0;
    while (true)
    {
        tempSensors.Read(); // note, this causes approx 700ms delay
        vTaskDelay((maximetDataIntervalSeconds * 1000 - 700) / portTICK_PERIOD_MS);
        float boardtemp = tempSensors.GetBoardTemp();
        float watertemp = tempSensors.GetWaterTemp();


        simulator.SetTemperature(watertemp);

        unsigned int uptimeSeconds = (unsigned int)(esp_timer_get_time() / 1000000); // seconds since start
        if (uptimeSeconds - lastSendTimestamp >= httpPostDataIntervalSeconds)
        {
            lastSendTimestamp = uptimeSeconds;
            sendData.PrepareHttpPost(5000, 70, boardtemp, watertemp, true, mOnlineMode, tempSensorRomCodes);

            int sendViaWifiTries = 10;
            while (sendViaWifiTries--)
            {
                if (mWifi.IsConnected() && sendData.PerformHttpPost())
                {
                    break;
                }
                else
                {
                    vTaskDelay(1000 / portTICK_PERIOD_MS);
                    mWifi.Reconnect();
                    ESP_LOGW(tag, "Retrying sending via wifi. Remaining attempts: %i", sendViaWifiTries);
                }
            }
        }
    }
}
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

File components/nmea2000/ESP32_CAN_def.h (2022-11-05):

/**
 * @section License
 *
 * The MIT License (MIT)
 *
 * Copyright (c) 2017, Thomas Barth, barth-dev.de
 *
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
 * THE SOFTWARE IS PROVIDED "AS IS", WITHOUT WARRANTY OF ANY KIND,
 * EXPRESS OR IMPLIED, INCLUDING BUT NOT LIMITED TO THE WARRANTIES OF
 * MERCHANTABILITY, FITNESS FOR A PARTICULAR PURPOSE AND
 * NONINFRINGEMENT. IN NO EVENT SHALL THE AUTHORS OR COPYRIGHT HOLDERS
 * BE LIABLE FOR ANY CLAIM, DAMAGES OR OTHER LIABILITY, WHETHER IN AN
 * ACTION OF CONTRACT, TORT OR OTHERWISE, ARISING FROM, OUT OF OR IN
 * CONNECTION WITH THE SOFTWARE OR THE USE OR OTHER DEALINGS IN THE
 * SOFTWARE.
 */

#ifndef __DRIVERS_CAN_REGDEF_H_
#define __DRIVERS_CAN_REGDEF_H_

#ifdef __cplusplus
extern "C" {
#endif

typedef enum  {
	CAN_SPEED_100KBPS=100, 				/**< \brief CAN Node runs at 100kBit/s. */
	CAN_SPEED_125KBPS=125, 				/**< \brief CAN Node runs at 125kBit/s. */
	CAN_SPEED_250KBPS=250, 				/**< \brief CAN Node runs at 250kBit/s. */
	CAN_SPEED_500KBPS=500, 				/**< \brief CAN Node runs at 500kBit/s. */
	CAN_SPEED_800KBPS=800, 				/**< \brief CAN Node runs at 800kBit/s. */
	CAN_SPEED_1000KBPS=1000				/**< \brief CAN Node runs at 1000kBit/s. */
}CAN_speed_t;

/**
 * \brief CAN frame type (standard/extended)
 */
typedef enum {
	CAN_frame_std=0, 						/**< Standard frame, using 11 bit identifer. */
	CAN_frame_ext=1 						/**< Extended frame, using 29 bit identifer. */
}CAN_frame_format_t;

/**
 * \brief CAN RTR
 */
typedef enum {
	CAN_no_RTR=0, 							/**< No RTR frame. */
	CAN_RTR=1 								/**< RTR frame. */
}CAN_RTR_t;

/** \brief Frame information record type */
typedef union{uint32_t U;					/**< \brief Unsigned access */
	 struct {
		uint8_t 			DLC:4;        	/**< \brief [3:0] DLC, Data length container */
		unsigned int 		unknown_2:2;    /**< \brief \internal unknown */
		CAN_RTR_t 			RTR:1;          /**< \brief [6:6] RTR, Remote Transmission Request */
		CAN_frame_format_t 	FF:1;           /**< \brief [7:7] Frame Format, see# CAN_frame_format_t*/
		unsigned int 		reserved_24:24;	/**< \brief \internal Reserved */
	} B;
} CAN_FIR_t;

/** \brief Start address of CAN registers */
#define MODULE_CAN              					((volatile CAN_Module_t    *)0x3ff6b000)

/** \brief Get standard message ID */
#define _CAN_GET_STD_ID								(((uint32_t)MODULE_CAN->MBX_CTRL.FCTRL.TX_RX.STD.ID[0] << 3) | \
													(MODULE_CAN->MBX_CTRL.FCTRL.TX_RX.STD.ID[1] >> 5))

/** \brief Get extended message ID */
#define _CAN_GET_EXT_ID   (((uint32_t)MODULE_CAN->MBX_CTRL.FCTRL.TX_RX.EXT.ID[0] << 21) | \
													(MODULE_CAN->MBX_CTRL.FCTRL.TX_RX.EXT.ID[1] << 13) | \
													(MODULE_CAN->MBX_CTRL.FCTRL.TX_RX.EXT.ID[2] << 5) | \
													(MODULE_CAN->MBX_CTRL.FCTRL.TX_RX.EXT.ID[3] >> 3 ))

/** \brief Set standard message ID */
#define _CAN_SET_STD_ID(x)							MODULE_CAN->MBX_CTRL.FCTRL.TX_RX.STD.ID[0] = ((x) >> 3);	\
													MODULE_CAN->MBX_CTRL.FCTRL.TX_RX.STD.ID[1] = ((x) << 5);

/** \brief Set extended message ID */
#define _CAN_SET_EXT_ID(x)							MODULE_CAN->MBX_CTRL.FCTRL.TX_RX.EXT.ID[0] = ((x) >> 21);	\
													MODULE_CAN->MBX_CTRL.FCTRL.TX_RX.EXT.ID[1] = ((x) >> 13);	\
													MODULE_CAN->MBX_CTRL.FCTRL.TX_RX.EXT.ID[2] = ((x) >> 5);	\
													MODULE_CAN->MBX_CTRL.FCTRL.TX_RX.EXT.ID[3] = ((x) << 3);	\

/** \brief Interrupt status register */
typedef enum  {
	__CAN_IRQ_RX=			BIT(0),					/**< \brief RX Interrupt */
	__CAN_IRQ_TX=			BIT(1),					/**< \brief TX Interrupt */
	__CAN_IRQ_ERR=			BIT(2),					/**< \brief Error Interrupt */
	__CAN_IRQ_DATA_OVERRUN=	BIT(3),					/**< \brief Date Overrun Interrupt */
	__CAN_IRQ_WAKEUP=		BIT(4),					/**< \brief Wakeup Interrupt */
	__CAN_IRQ_ERR_PASSIVE=	BIT(5),					/**< \brief Passive Error Interrupt */
	__CAN_IRQ_ARB_LOST=		BIT(6),					/**< \brief Arbitration lost interrupt */
	__CAN_IRQ_BUS_ERR=		BIT(7),					/**< \brief Bus error Interrupt */
}__CAN_IRQ_t;


/** \brief OCMODE options. */
typedef enum  {
	__CAN_OC_BOM=			0b00,					/**< \brief bi-phase output mode */
	__CAN_OC_TOM=			0b01,					/**< \brief test output mode */
	__CAN_OC_NOM=			0b10,					/**< \brief normal output mode */
	__CAN_OC_COM=			0b11,					/**< \brief clock output mode */
}__CAN_OCMODE_t;
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

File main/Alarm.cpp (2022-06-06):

//#define LOG_LOCAL_LEVEL ESP_LOG_DEBUG

#include "Alarm.h"
#include "freertos/FreeRTOS.h"
#include "freertos/task.h"
#include "esp_system.h"
#include "esp_event.h"
#include "esp_log.h"
#include "math.h"
#include <cmath>
#include "stdlib.h"
#include "GeoUtil.h"

static const char tag[] = "Alarm";

void fAlarmTask(void *pvParameter)
{
    ((Alarm *)pvParameter)->AlarmTask();
    vTaskDelete(NULL);
}

void Alarm::Start()
{
    xTaskCreate(&fAlarmTask, "Alarm", 1024 * 4, this, ESP_TASK_MAIN_PRIO, NULL); // large stack is needed
}

void Alarm::AlarmTask()
{
    if (mrConfig.mbAlarmSound)
    {
        gpio_config_t gpioConfig;
        gpioConfig.mode = GPIO_MODE_OUTPUT;
        gpioConfig.intr_type = GPIO_INTR_DISABLE;
        gpioConfig.pull_down_en = GPIO_PULLDOWN_DISABLE;
        gpioConfig.pull_up_en = GPIO_PULLUP_DISABLE;
        gpioConfig.pin_bit_mask = (1ULL<<mGpioBuzzer);
        gpio_config(&gpioConfig);
        gpio_set_drive_capability(mGpioBuzzer, GPIO_DRIVE_CAP_3);
        ESP_LOGI(tag, "Buzzer enabled on GPIO%d", mGpioBuzzer);
        BuzzerOff();
    }

    if (mrConfig.miAlarmRadius < 10)
    {
        // ESP_LOGE(tag, "Alarm Radius too small")
    }

    static const short ARMING_SECONDS = 30;   // 60 counts = 60 seconds
    static const short COOLDOWN_SECONDS = 60; // 30 seconds
    static const short MAXALARMACTIVESECONDS = 300; // 5 minutes

    unsigned int countArming = 0;
    unsigned int countTilt = 0;
    unsigned int countOrient = 0;
    unsigned int countUnplugged = 0;
    unsigned int countGeoFence = 0;

    unsigned int alarmTriggers = 0;

    int timestampAlarmTriggered = 0;
    int timestampAlarmCooldown = 0;
    while (true)
    {
        Data data;
        unsigned short absAvgTilt = 0;
        unsigned int geoDislocation = 0;

        if (mrDataQueue.GetAlarmData(data, 3))
        {

            // 60 seconds of data before arming system
            if (countArming < ARMING_SECONDS)
            {
                //ESP_LOGI(tag, "Arming %d", countArming);
                countArming++;
            }
            else if (countArming == ARMING_SECONDS)
            {
                countArming++;
                ESP_LOGW(tag, "ARMED! Buzzer %s", mrConfig.mbAlarmSound ? "activated" : "muted");
            }

            countUnplugged = 0;

            // average the individual angles, so that a rocking buoy is averaging upright
            // however, when a malicious activity happens, the tilt is likely to happen steady in one direction
            float avgXTilt = movAvgTiltXmm(data.xtilt);
            float avgYTilt = movAvgTiltYmm(data.ytilt);
            absAvgTilt = abs(avgXTilt) + abs(avgYTilt);

            #if LOG_LOCAL_LEVEL >= LOG_DEFAULT_LEVEL_DEBUG || CONFIG_LOG_DEFAULT_LEVEL >= LOG_DEFAULT_LEVEL_DEBUG
                unsigned short absTilt = abs(data.xtilt) + abs(data.ytilt);
                ESP_LOGD(tag, "Tilt angles: xtilt=%d, ytilt=%d tilt=%d avgtilt=%d", data.xtilt, data.ytilt, absTilt, absAvgTilt);
            #endif 



            // if zorient is -1 then maximet is tilted upside down (more than 90° tilt)
            if (data.zorient < 0)
            {
                countOrient++;
                //ESP_LOGD(tag, "UPSIDE DOWN!");
            }
            else
            {
                countOrient = 0;
            }

            // the sum of both tilts is max 90°
            if (absAvgTilt > miTiltThreshold)
            {
                countTilt++;
                //ESP_LOGD(tag, "TILT! %d°/%d° (%d°)", data.xtilt, data.ytilt, absAvgTilt);
            }
            else
            {
                countTilt = 0;
            }

            // geofence
            if (mrConfig.mdAlarmLatitude && mrConfig.mdAlarmLongitude && data.lat && data.lon && !isnan(mrConfig.mdAlarmLatitude) && !isnan(mrConfig.mdAlarmLongitude) && !isnan(data.lat) && !isnan(data.lon))
            {
                geoDislocation = geoDistance(mrConfig.mdAlarmLatitude, mrConfig.mdAlarmLongitude, data.lat, data.lon);
                if (geoDislocation > mrConfig.miAlarmRadius)
                {
                    // if bogus distance of >100km reset geofence
                    if (geoDislocation > 100000)
                    {
                        countGeoFence = 0;
                    }
                    else
                    {
                        countGeoFence++;
                    }
                }
                else
                {
                    countGeoFence = 0;
                }
            }

            if (countTilt >= 1)
            {
                alarmTriggers |= TILT;
            }

            if (countOrient >= 9)
            {
                alarmTriggers |= ORIENT;
            }

            if (countGeoFence >= 5)
            {
                alarmTriggers |= GEOFENCE;
            }
        }
        else
        {
            countUnplugged++;
        }

        if (countUnplugged >= 2)
        {
            alarmTriggers |= UNPLUGGED;
        }

        if (countArming < ARMING_SECONDS)
        {
            // reset triggers during arming phase, extend arming --> arm only if all is good
            if (countUnplugged || countGeoFence || countOrient || countTilt || alarmTriggers) {
                countArming = 0;
                alarmTriggers = 0;
                countGeoFence = 0;
                countUnplugged = 0;
                countOrient = 0;
                countTilt = 0;
            }
            continue;
        }
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

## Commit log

2021-03-12 netif driver basics
2021-03-13 modem driver work
2021-03-14 ppp switching cleanup
2021-03-20 refactoring for SIM7600
    [cpplint.cfg]
2021-03-23 still esp_tls_transport issues with >115200 baud
    [Cellular.cpp, Esp32WeatherBuoy.cpp]
2021-03-25 level shifter and voltage working
2021-03-28 adding ds18b20 temperature sensors
2021-03-29 improved temp sensor detection
2021-04-22 current metering
2021-04-24 low power mode and ppp reconnect tests
2021-05-06 watchdog with tasknotify, adaptivemeasure for ADC
2021-05-17 fixed missing cdir data
    [Esp32WeatherBuoy.cpp]
2021-07-19 docu update
    [maximet stand.stl, solarpanel blind cable plug 6mm.stl, weatherbuoy battery lid.stl]
2021-07-19 more cad
2021-08-01 wiring diagram update
2021-12-13 partiall success cheating garmin
    [weatherbuoypcbeagle.brd]
2021-12-26 send sample data to display
2021-12-28 correcting gps data formatting
    [Esp32WeatherBuoy.cpp]
2022-01-30 speed short term average
    [Maximet.cpp]
2022-02-08 fixed cellular serial read
    [Cellular.cpp]
2022-02-11 UART IRAM and more robust cellular
2022-02-26 update doc and final pcb
    [weatherbuoy pcb.brd, weatherbuoypcbeagle.brd]
2022-02-28 cleaned up switch ppp to commandline mode
    [gps.csv]
2022-03-06 maximet output string corrections
    [MaximetSimulator.cpp]
2022-03-12 modem error handling improvements
    [Cellular.cpp, Esp32WeatherBuoy.cpp]
2022-03-16 setting apn; correcting windspeed while avg building
    [Cellular.cpp, Esp32WeatherBuoy.cpp, Maximet.cpp]
2022-03-17 finally fixed bug with stuck modem comms
    [Cellular.cpp, Maximet.cpp]
2022-03-17 RESET input buffers cleanup
    [Cellular.cpp]
2022-03-18 uart pining for wakeup modem v220318.1625
2022-03-19 additional checks for broken connection
    [Cellular.cpp]
2022-03-20 minor simulator and diagnostics fixes
    [MaximetSimulator.cpp]
2022-03-23 recreate netif on error v220323.1504
    [Cellular.cpp]
2022-03-26 additional safety precautions due to driver crashing v220326.1945
    [Cellular.cpp]
2022-03-29 reset UART only in eventqueue v220329.2017
    [Cellular.cpp]
2022-04-10 release candidate, fixed cmdmode race condition v220410.1152
    [Cellular.cpp, Esp32WeatherBuoy.cpp, Maximet.cpp]
2022-04-10 fixed SMS csv-phone number sending v220410.1919
    [Cellular.cpp, Esp32WeatherBuoy.cpp]
2022-06-18 fix winddirection when GPS is not available on buoykammer
    [Maximet.cpp]
2022-06-19 workarounds for GPS outage
    [Maximet.cpp]
2022-06-24 wmo calc if gps fix not avail
    [Maximet.cpp]
2022-09-06 added U/V to velocityvector
2022-11-05 changed powering NMEA from GPIO, updated NMEA library
2022-12-20 reassembly of ip packets fixes TCP issues
    [Cellular.cpp]
2023-04-02 added power cycling the modem to help recover from error condistions
    [Cellular.cpp, Esp32WeatherBuoy.cpp]
2023-04-02 fixing maximetsimulator and avoiding IPv6 with ppp
    [Cellular.cpp, Esp32WeatherBuoy.cpp, MaximetSimulator.cpp]
2023-04-03 added additional diagnostics info and physical modem reboot
    [Cellular.cpp, Esp32WeatherBuoy.cpp, Maximet.cpp]
2023-04-04 minor maximetsimulator fixes handling %%
    [Cellular.cpp, Esp32WeatherBuoy.cpp, Maximet.cpp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]
2023-07-03 added config feature to reset maximet to defaults
    [Maximet.cpp, Maximet.h]
2024-06-30 looking at temperature sensor
2024-07-01 option to configure primary temperature sensor
